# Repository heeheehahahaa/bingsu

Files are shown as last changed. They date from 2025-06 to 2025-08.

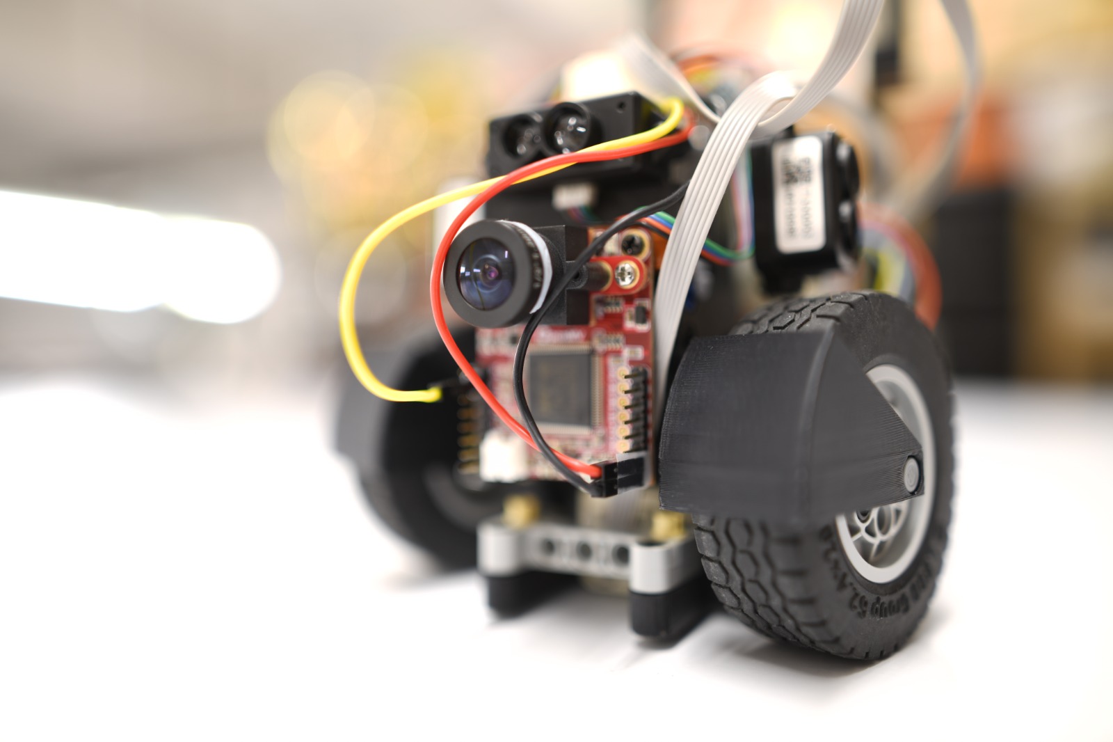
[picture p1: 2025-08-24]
v-photos/WhatsApp Image 2025-08-17 at 16.47.16.jpeg

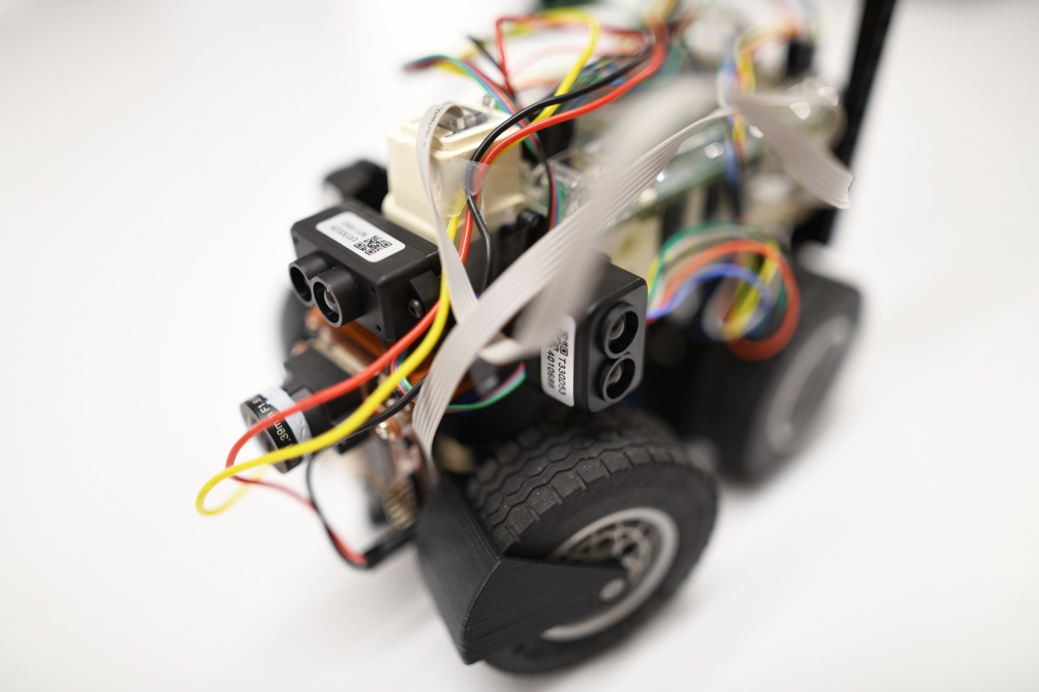
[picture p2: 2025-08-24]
v-photos/WhatsApp Image 2025-08-17 at 16.47.00.jpeg

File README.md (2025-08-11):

# Engineering Materials

This repository holds the engineering materials for a self-driving vehicle model competing in the WRO Future Engineers competition for the 2025 season.   

# Introduction
This document details the design and implementation of a robot built for a competition, utilising a custom 3D-printed chassis and a variety of off-the-shelf electronic components. The robot is designed using Autodesk Fusion 360 and manufactured with Fused Filament Fabrication (FFF) 3D printing using Polylactic Acid (PLA). It incorporates LEGO MINDSTORMS EV3 motors,  Benewake TFmini and TF luna LiDAR sensors, a JoinMax JMP-BE-2617 Compass, and an OpenMV H7 camera.

# Our solution
Design and Manufacturing

- Software: Autodesk Fusion 360 was used for both Computer-Aided Design and Computer-Aided Manufacturing
- Printing Technology: Fused Filament Fabrication (FFF) with Polylactic Acid (PLA) filament was chosen for its affordability, versatility, and suitability for structural components.

Key Components

- The compass mount is mounted as high as possible to prevent magnetic interference with other parts of the robot/disturbance from environmental factors
- Drive base structure attaches the front motors and wheels to other parts of the robot, including the back wheels and other mounts. This connects to the medium motor for driving the robot, the pivot points for the steering mechanism, and additional points to mount sensors at the front. The front and back parts are connected via a thin structure which is not possible to do with LEGO parts. This gives the robot the ability to steer at larger angles, reducing the turning radius and making the robot more agile. 
- The wheel mount attaches the front wheels to the base structure of the robot.
- There is an integrated 40-tooth equivalent spur gear which is driven by an 8-tooth gear attached to an EV3 Medium motor
- The sensor mount is placed at the back of the robot, attaching the back TF mini to the body of the robot.  We placed it such that the majority of the field-of-view (FOV) lies on the wall, even at the furthest distance.
- Motor mount attaches a medium motor downwards which controls the steering wheels. We decided to mount it lower to be certain that it is able to range against the 10cm tall walls.
- Camera mount attaches the camera to the front of the robot, below the front ToF. It is kept low, allowing the camera to detect the blocks in the obstacle challenge more easily. 

Microcontroller

- EVN Alpha Advantages: Compared to LEGO MINDSTORMS EV3 and NXT controllers, the EVN Alpha offers 64 holes on 5 sides for mounting, is more compact, and features a USB-C port for charging and programming. It also has 16 I2C channels, overcoming the 4-port constraint of other controllers.

Motors and Gearbox

- Motors: Two LEGO MINDSTORMS EV3 medium motors are used for their light weight and high speed. One motor drives the robot through a complex gearbox setup, and the other handles steering with high precision.
- Gearbox: The gearbox includes a combination of bevel gears and planetary gears to achieve a total reduction ratio of 14:5. This design optimises the robot’s speed and stability.
- Wheels: 62.4mm LEGO TECHNIC wheels provide high friction and stability, crucial for rapid changes in direction and precise movement.

Steering Mechanism
- We implemented Ackermann geometry to ensure accurate and slip-free turning by adjusting the speeds of the left and right wheels according to their respective radii during turns.

Power Source

- Battery: The robot uses two 18650 cells connected in series, providing 8.4V. The batteries are capable of lasting over an hour of continuous operation due to their high discharge rate and capacity.
- Regulation: On-board regulators supply 3.3V and 5V to various components, with ample current capability to support all sensors and peripherals.

Sensors

- TF Mini-S: Mounted at the front and back for distance measurement
- TF luna: Two sensors placed on the sides for accurate distance measurement with a range of up to 2 metres.
- JoinMax BE-2617 Compass: Provides accurate heading data and adjusts the robot’s movement to correct any deviation.
- OpenMV H7 Camera: Positioned at the front to detect objects such as traffic lights and blocks

Challenges

- Wall Tracking: The robot maintains a fixed distance from the wall using proportional control based on the current and target distances.
- Turns: The robot sets a fixed heading to navigate turns based on block positions, adjusting its movement as needed.

Software Functionality

- State Management: The robot operates in different states (Cases 0-8) to manage initial positioning, wall tracking, turning, and responding to specific blocks in the obstacle challenge.

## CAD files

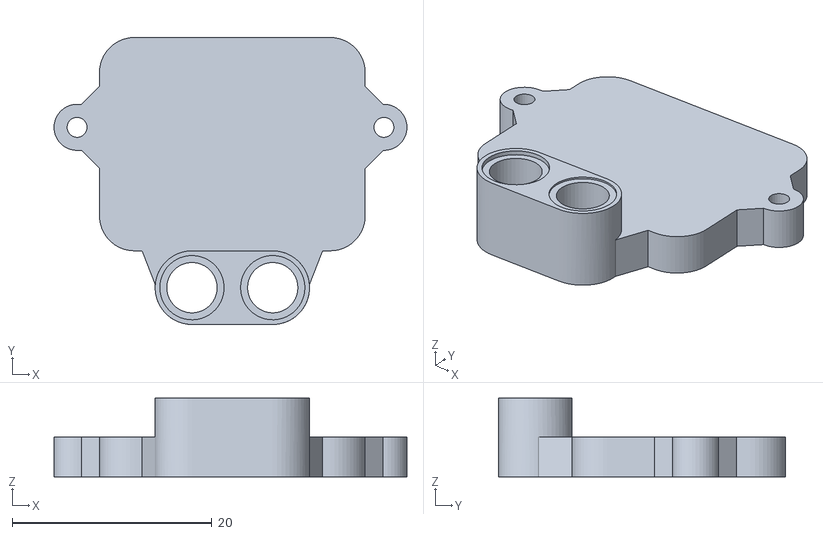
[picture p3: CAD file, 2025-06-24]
models/usmount.stl
35.4 x 28.7 x 7.88

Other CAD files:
models/frontsensormount.f3d

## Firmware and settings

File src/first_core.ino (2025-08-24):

#include <TFLI2C.h>
const int16_t  tfAddr = TFL_DEF_ADR;

EVNAlpha board;

TFLI2C rightSensor;
TFLI2C leftSensor;

bool read_right_tof = true;

byte tof_message_state = 0;
byte tof_dist_1 = 0;
byte tof_dist_2 = 0;
bool tof_available = false;


byte back_tof_message_state = 0;
byte back_tof_dist_1 = 0;
byte back_tof_dist_2 = 0;
bool back_tof_available = false;

unsigned long long last_print_millis = 0;
unsigned long long last_tofread_millis = 0;
int temp;
#define DTOR(a) (float)a * PI / 180.0 

#define CORRECTED_DISTANCE(d) d * cos(DTOR(snapped_heading))
#include <SoftwareSerial.h>
SoftwareSerial camSerial(11,10);

void setup() {
  // put your setup code here, to run once:  
  Serial.begin(921600);
  //Serial.begin(9600);
  Serial.println("Initializing...");
  camSerial.begin(115200);
  board.begin();
  board.setPort(9);

  driveMotor.begin();

  Serial1.begin(115200);
  Serial1.write((uint8_t)0x42);
  Serial1.write((uint8_t)0x57);
  Serial1.write((uint8_t)0x02);
  Serial1.write((uint8_t)0x00);
  Serial1.write((uint8_t)0x00);
  Serial1.write((uint8_t)0x00);
  Serial1.write((uint8_t)0x01);
  Serial1.write((uint8_t)0x06);
  delay(100);

  Serial2.begin(115200);
  Serial2.write((uint8_t)0x42);
  Serial2.write((uint8_t)0x57);
  Serial2.write((uint8_t)0x02);
  Serial2.write((uint8_t)0x00);
  Serial2.write((uint8_t)0x00);
  Serial2.write((uint8_t)0x00);
  Serial2.write((uint8_t)0x01);
  Serial2.write((uint8_t)0x06);
  delay(100);

  core0_ready = true;

  while (!core1_ready)
    ;
}

void loop() {
  // put your main code here, to run repeatedly:
  while (camSerial.available()) {
    cam_state = camSerial.read() - '0';
  }
  // READ COMPASS
  if (Wire1.requestFrom(0x3B, 2) == 2) {
    while (Wire1.available() < 2)
      ;
    heading = Wire1.read() * 255 + Wire1.read();
    snapped_heading = heading % 90 > 45 ? (heading % 90) - 90 : heading % 90;
  } else {
    Serial.println("failed");
  }

  // READ FRONT TOF
  while (Serial1.available()) {
    byte curChar = Serial1.read();
    switch (tof_message_state) {
      case 0:
        // wait for first 0x59
        tof_message_state = (curChar == 0x59) ? 1 : 0;
        break;
      case 1:
        // wait for second 0x59
        tof_message_state = (curChar == 0x59) ? 2 : 0;
        break;
      case 2:
        tof_dist_1 = curChar;
        tof_message_state++;
        break;
      case 3:
        tof_dist_2 = curChar;
        tof_message_state++;
        break;
      default:
        // reset to base state
        tof_message_state = 0;
        tof_available = true;
        break;
    }
  }

  if (tof_available) {
    tof_available = false;
    int temp = (tof_dist_2 << 8) + tof_dist_1;
    tof_dist = temp <= 300 ? temp : 0;
    tof_dist_corrected = CORRECTED_DISTANCE(tof_dist);
  }

  // READ BACK TOF
  while (Serial2.available()) {
    byte curChar = Serial2.read();
    switch (back_tof_message_state) {
      case 0:
        // wait for first 0x59
        back_tof_message_state = (curChar == 0x59) ? 1 : 0;
        break;
      case 1:
        // wait for second 0x59
        back_tof_message_state = (curChar == 0x59) ? 2 : 0;
        break;
      case 2:
        back_tof_dist_1 = curChar;
        back_tof_message_state++;
        break;
      case 3:
        back_tof_dist_2 = curChar;
        back_tof_message_state++;
        break;
      default:
        // reset to base state
        back_tof_message_state = 0;
        back_tof_available = true;
        break;
    }
  }

  if (back_tof_available) {
    back_tof_available = false;
    int temp = (back_tof_dist_2 << 8) + back_tof_dist_1;
    back_tof_dist = temp <= 300 ? temp : 0;
    back_tof_dist_corrected = CORRECTED_DISTANCE(back_tof_dist);
  }

  // READ LEFT AND RIGHT TOF
  if (millis() - last_tofread_millis > 10) {
  board.setPort (1);
  if( rightSensor.getData(tfRightDist, tfAddr)) // If read okay...
    {
        //Serial.print("rightDist: ");
        //Serial.println(tfRightDist);          // print the data...
        right_tof_dist_corrected = tfRightDist < 300 ? CORRECTED_DISTANCE(tfRightDist)*10 : 8191;
    }
    else rightSensor.printStatus();           // else, print error.
  
  board.setPort (3);
      if(leftSensor.getData(tfLeftDist, tfAddr)) // If read okay...
    {
        //Serial.print("leftDist: ");
        //Serial.println(tfLeftDist);          // print the data...
        left_tof_dist_corrected = tfLeftDist < 300 ? CORRECTED_DISTANCE(tfLeftDist)*10 : 8191;
    }
    else leftSensor.printStatus();           // else, print error.
  
    last_tofread_millis = millis();
  }

  
  if (millis() - last_print_millis >= PRINT_DELAY) {
    Serial.print(tof_dist_corrected);
    Serial.print(" , ");
    Serial.print(tof_dist);
    Serial.print("f\t");

    Serial.print(back_tof_dist_corrected);
    Serial.print(" , ");
    Serial.print(back_tof_dist);
    Serial.print("b\t");

    Serial.print(left_tof_dist_corrected);
    Serial.print(" , ");
    Serial.print(tfLeftDist);
    Serial.print("l\t");

    Serial.print(right_tof_dist_corrected);
    Serial.print(" , ");
    Serial.print(tfRightDist);
    Serial.print("r\t");

    Serial.print(snapped_heading);
    Serial.print(" , ");
    Serial.print(heading);
    Serial.print("h\t");

    Serial.print(pulseCount);
    Serial.print("p\t");
    
    Serial.print(cam_state);
    Serial.print("c\t");

    Serial.println();
    last_print_millis = millis();
  }
  
}

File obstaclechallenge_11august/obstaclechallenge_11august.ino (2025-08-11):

//change 300 to 1000 for turn

#include <EVN.h>
EVNMotor driveMotor(4, EV3_MED);

volatile int pulseCount;  // Rotation step count
int SIG_A = 0;            // Pin A output
int SIG_B = 0;            // Pin B output
int lastSIG_A = 0;        // Last state of SIG_A
int lastSIG_B = 0;        // Last state of SIG_B
const int Pin_A = 14;     // Interrupt pin (digital) for A (change your pins here)
const int Pin_B = 15;     // Interrupt pin (digital) for B

void A_CHANGE() {              // Interrupt Service Routine (ISR)
  detachInterrupt(0);          // Important
  SIG_A = digitalRead(Pin_A);  // Read state of A
  SIG_B = digitalRead(Pin_B);  // Read state of B

  if ((SIG_B == SIG_A) && (lastSIG_B != SIG_B)) {
    pulseCount--;  // Counter-clockwise rotation
    lastSIG_B = SIG_B;
  }

  else if ((SIG_B != SIG_A) && (lastSIG_B == SIG_B)) {
    pulseCount++;                   // Clockwise rotation
    lastSIG_B = SIG_B > 0 ? 0 : 1;  // Save last state of B
  }
  attachInterrupt(digitalPinToInterrupt(Pin_A), A_CHANGE, CHANGE);
}

#define DRIVE driveMotor.runPWM(-100)
#define STOPP driveMotor.stop()

#define PRINT_DELAY 1000

#define STEER_CENTER 283

volatile bool core0_ready = false;
volatile bool core1_ready = false;

int16_t tfRightDist;
int16_t tfLeftDist;


volatile int tof_dist = 999;
volatile int back_tof_dist = 999;
volatile int heading = 0;
int snapped_heading = 0;

int tof_dist_corrected = 999;
int back_tof_dist_corrected = 999;
int right_tof_dist_corrected = 999;
int left_tof_dist_corrected = 999;

int steer_right_bound = 0;
int steer_left_bound = 0;
int corner = 1;
int initial_left = 150;
int initial_back = 50;

byte cam_state = 255;

int steerOffset = 180;

int initialPosition;

bool ccw = false; 

void runPosition(int targetPosition) {
  int positionError = pulseCount - targetPosition;  //(headingError * 5.0) - (steer.getPosition() - STEER_CENTER);
  //Serial.println(positionError);
  int pwmRun = constrain(positionError * 30, -250, 250);
  //Serial.println(pwmRun);
  if (positionError > 0) {
    // turn cw
    digitalWrite(23, HIGH);
    analogWrite(22, 255 - pwmRun);
  } else {
    //turn ccw
    digitalWrite(22, HIGH);
    analogWrite(23, 255 + pwmRun);
  }
}

void trackWall(int wallDist) {
  int leftDistError = left_tof_dist_corrected != 2191 && abs(snapped_heading) < 30 ? wallDist - left_tof_dist_corrected : 0;
  int targetHeading = constrain(leftDistError / 5.0, -30.0, 30.0);
  int headingError = targetHeading - snapped_heading;
  runPosition(steer_right_bound + steerOffset - (headingError * 6.0));
  DRIVE;
}

void trackWallRight(int wallDist) {
  int rightDistError = right_tof_dist_corrected != 2191 && abs(snapped_heading) < 30 ? right_tof_dist_corrected - wallDist : 0;
  int targetHeading = constrain(rightDistError / 5.0, -30.0, 30.0);
  int headingError = targetHeading - snapped_heading;
  runPosition(steer_right_bound + steerOffset - (headingError * 6.0));
  DRIVE;
}

void trackHeading(int targetHeading) {
  //int leftDistError = left_tof_dist_corrected != 2191 && abs(snapped_heading) < 30 ? 150 - left_tof_dist_corrected : 0;
  //int targetHeading = constrain(leftDistError / 5.0, -30.0, 30.0);
  int headingError = targetHeading - snapped_heading;
  //Serial.println(targetHeading);
  runPosition(steer_right_bound + steerOffset - (headingError * 6.0));
  DRIVE;
}
void trackHeadingReverse(int targetHeading) {
  //int leftDistError = left_tof_dist_corrected != 2191 && abs(snapped_heading) < 30 ? 150 - left_tof_dist_corrected : 0;
  //int targetHeading = constrain(leftDistError / 5.0, -30.0, 30.0);
  int headingError = targetHeading - snapped_heading;
  //Serial.println(targetHeading);
  runPosition(steer_right_bound + steerOffset - (headingError * 6.0));
  driveMotor.runPWM(100);
}

void reverse(int targetHeading) {
  int headingError = targetHeading - snapped_heading;
  runPosition(steer_right_bound + steerOffset + (headingError * 6.0));
  driveMotor.runPWM(100);
}

void leftTurn(int revert = 0) {
  int nextHeading = (36000 - ((corner - revert) * 90)) % 360;
  DRIVE;
  while (abs(heading - nextHeading) > 5) {
    runPosition(steer_right_bound + (steerOffset * 2.1));
  }
  STOPP;
  delay(1000);
}

void leftReverseTurn(int revert = 0) {
  int nextHeading = (36000 - ((corner - revert) * 90)) % 360;
  while (abs(heading - nextHeading) > 5) {
    runPosition(steer_right_bound + (steerOffset * 2.1));
    driveMotor.runPWM(100);
  }
  STOPP;
  delay(1000);
}

void rightTurn(int revert = 0) {
  int nextHeading = (36000 + ((corner - revert) * 90)) % 360;
  DRIVE;
  while (abs(heading - nextHeading) > 5) {
    runPosition(steer_right_bound + steerOffset - (steerOffset * 0.88));
  }
  STOPP;
  delay(1000);
}

void rightReverseTurn(int revert = 0) {
  int nextHeading = (36000 + ((corner - revert) * 90)) % 360;
  while (abs(heading - nextHeading) > 5) {
    runPosition(steer_right_bound + steerOffset - (steerOffset * 0.88));
    driveMotor.runPWM(100);
  }
  STOPP;
  delay(1000);
}

void left(int anglechange = 30) {
  int initialHeading = snapped_heading;
  DRIVE;
  while (abs(snapped_heading - initialHeading) < anglechange) {
    Serial.println(abs(snapped_heading - initialHeading));
    runPosition(steer_right_bound + 200 + 100);
  }
  STOPP;
  delay(1000);
}

void right(int anglechange = 30) {
  int initialHeading = snapped_heading;
  DRIVE;
  while (abs(snapped_heading - initialHeading) < anglechange) {
    runPosition(steer_right_bound + 200 - 100);
  }
  STOPP;
  delay(1000);
}

void greenblock() {
  leftTurn(!ccw ? (-2*(corner-1)-1) : 0);
  left(15);
  rightTurn(ccw ? (-2*(corner-1)) : 0);
  right(15);
  leftTurn(1);
  initialPosition = driveMotor.getPosition();
  while (abs(driveMotor.getPosition() - initialPosition) < 888) { //change 90 during comp to see how uch to move back
    Serial.println(driveMotor.getPosition());
    reverse(0);
  }
}

void redblock(){
  rightTurn();
  right(15);
  leftTurn(1);
  driveMotor.stop();
  STOPP;
  //delay(1000);
  leftTurn();
  left(15);
  rightTurn(1);

  initialPosition = driveMotor.getPosition();
  while (abs(driveMotor.getPosition() - initialPosition) < 888) { //change 90 during comp to see how uch to move back
    Serial.println(driveMotor.getPosition());
    reverse(0);
  }
}
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
